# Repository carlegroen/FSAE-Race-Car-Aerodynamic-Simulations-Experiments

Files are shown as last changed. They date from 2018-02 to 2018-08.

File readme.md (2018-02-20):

# Bachelor Project: Aerodynamic design, simulations and experimental testing of a race car rear wing
- A bachelor project by Steffan Johan Kirk and Carl-Emil Grøn Christensen
- Supervisors: Jens Walther, Robert Mikkelsen

[Our formula student team's website](http://eventure.elektro.dtu.dk)

[Us in the competition]()

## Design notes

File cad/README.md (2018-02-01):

#CAD drawings for the project can be found here.

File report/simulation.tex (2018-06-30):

% !TEX root = main.tex
\chapter{Simulation}
\label{chap:simulations}

  The simulation will run in several parts. First, the wings relative placement between each other will be optimized in a 2-dimensional environment. This involves, $x$- and $y$-distance between the multi-element wings, angle of attack and height relative to the chassis to give a good estimate of the wings placement range. Secondly, a 3-dimensional analysis of the entire wing with endplates will be performed to compare with results from the wind tunnel test. %Endplate dimensions will be optimized, and further optimization of the height relative to the entire chassis to finalize the design and placement.

\section{Star-CCM+}
  Star-CCM+ was used to run the simulations of the wing first in the windtunnel for verification. As meshing and running the simulations were heavy computational tasks, the computations were run on the \emph{Niflheim Linux cluster supercomputer}, which is installed at the Department of Physics at DTU.

  The program numerically solves the Navier-Stokes equations, which are derived by the conservation of energy, mass and momentum through a volumetric flow. As Star-CCM+ uses the finite volume method, the equations are discretized to the conservative form: The in- and outgoing flux through a control volume must be conserved. Mathematically, this is expressed as:

  \begin{align}
    \frac{\delta}{\delta t} \iiint Q dV + \iint F dA = 0
  \end{align}
  Where $Q$ is the vector of the conserved variables (eg. $\rho =$ density), $F$ is the vector of fluxes(eg. $\rho u =$ mass flux, $\rho u^2 + p=$ momentum flux + pressure force) and $V$ is the control volume element and $A$ is the surface area of the control volume element. The turbulence model Star-CCM+ employs is a K-epsilon turbulence model which is the most commonly used in computational fluid dynamics. %The equations Star-CCM+ solves are the turbulent kinetic energy $k$:
  %\begin{align}
  %  \frac{\delta (\rho k)}{\delta t} + \frac{\delta (\rho k u_i)}{\delta x_i} &= \frac{\delta}{\delta x_j} \left(\frac{\mu_t}{\sigma_k}\frac{\delta k)}{\delta x_j}\right) + 2\mu_t E_{ij}E_{ij}-\rho \epsilon
  %  \intertext{and the dissipation $\epsilon$:}
  %  \frac{\delta (\rho \epsilon)}{\delta t} + \frac{\delta (\rho \epsilon u_i)}{\delta x_i} &= \frac{\delta}{\delta x_j} \left(\frac{\mu_t}{\sigma_\epsilon}\frac{\delta \epsilon)}{\delta x_j}\right) + C_{1\epsilon} \frac{\epsilon}{k} 2\mu_t E_{ij}E_{ij}-C_{2\epsilon}\rho \frac{\epsilon^2}{k}
  %\end{align}

  The reader interested in how Star-CCM+ works is referred to the \emph{User Guide Star-CCM+, version 13.02}.

\section{Mesh Generation}
\label{sec:mesh}

  The mesh has to be structured in accordance to best practice. Areas with high velocity and pressure gradients have to be dissolved in acceptable resolutions, in order to ensure correct results. Running an initial test on a generic mesh made it clear where the volume mesh requires greater resolution. Gradients are easily visible around the wing's leading edge, and generally around the solid bodies. Furthermore, aligning the mesh with the flow improves accuracy and rate of convergence. To determine the convergence of simulation results, six different mesh resolutions were used to examine the simulations for the wind tunnel setup with a wind velocity of $\SI{40}{\metre\per\second}$. Finding the minimum mesh resolution where results have converged with higher resolution results, means a minimum computation time can be achieved and thereby allowing for more simulations to be run.

  \begin{figure}
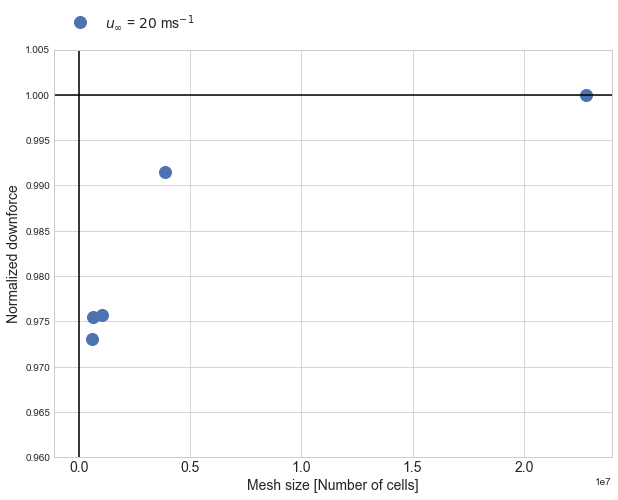
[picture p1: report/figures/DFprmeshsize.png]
    
    \caption{Normalized downforce as a function of mesh size. Plotted to see the convergence towards the same force.}
    \label{fig:DFprmeshsize}
  \end{figure}

  \begin{figure}
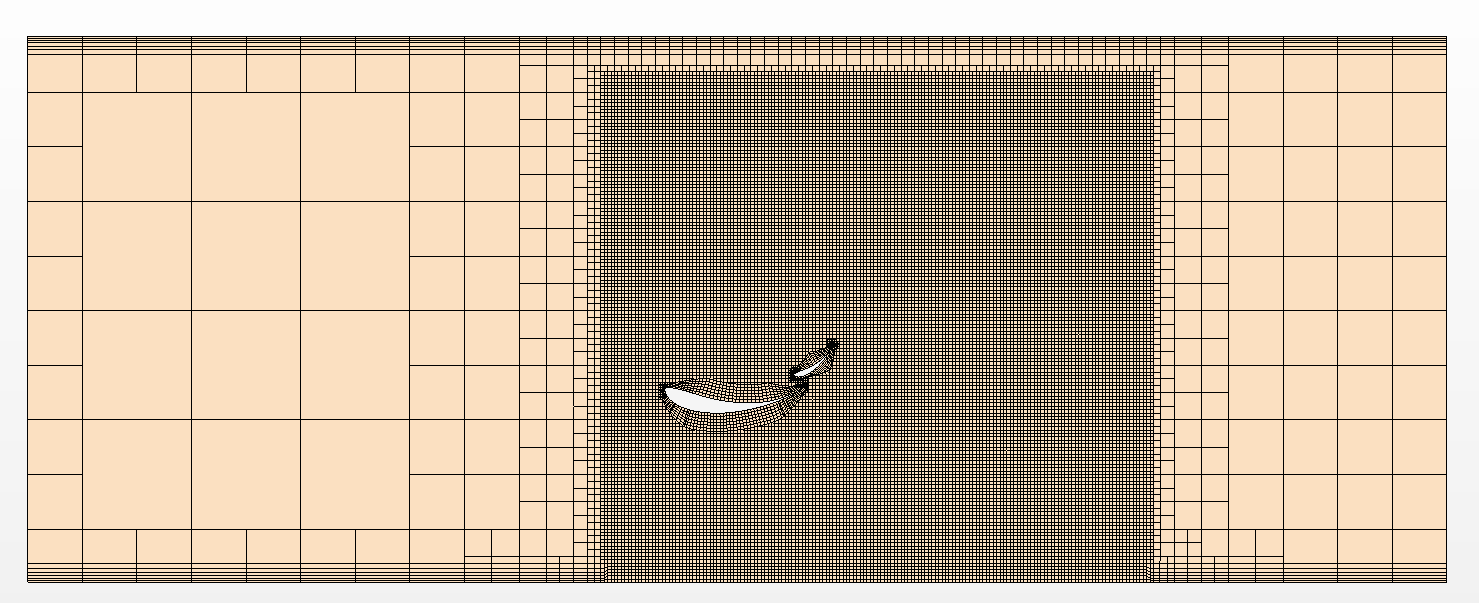
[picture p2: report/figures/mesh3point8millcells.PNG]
    
    \caption{2D cut through of the volume mesh used for simulations of the wind tunnel test. Mesh size is approximately $0.4 \cdot 10^{7}$ cells.}
    \label{fig:mesh3point8mill}
  \end{figure}

  Generating a mesh of correct size is done by sampling downforce over a range of mesh sizes. In figure \ref{fig:DFprmeshsize}, the normalized downforce is plotted as a function of the mesh size. The mesh independence study shows that the function converges to acceptable levels near the mesh size $\SI{.4E7}{}$, and serves as a good compromise between results and computing time.

  \section{Verification of Simulation Results}
  \label{sec:simulationcomparison}

  The data from the experimental test with the $\frac{1}{4}$ scale model was first plotted to obtain an idea of the surface pressure distribution on the test wing. An example of a mean over 3000 pressure readouts for a wind speed of $\SI{40}{\metre\per\second}$ is shown in figure \ref{fig:surfacepressureint}, with the standard deviation shown as error bars. Measurements were run in wind tunnel from $\SI{10}{\metre\per\second}$ to $\SI{60}{\metre\per\second}$ in steps of $\SI{10}{\metre\per\second}$.

  \begin{figure}
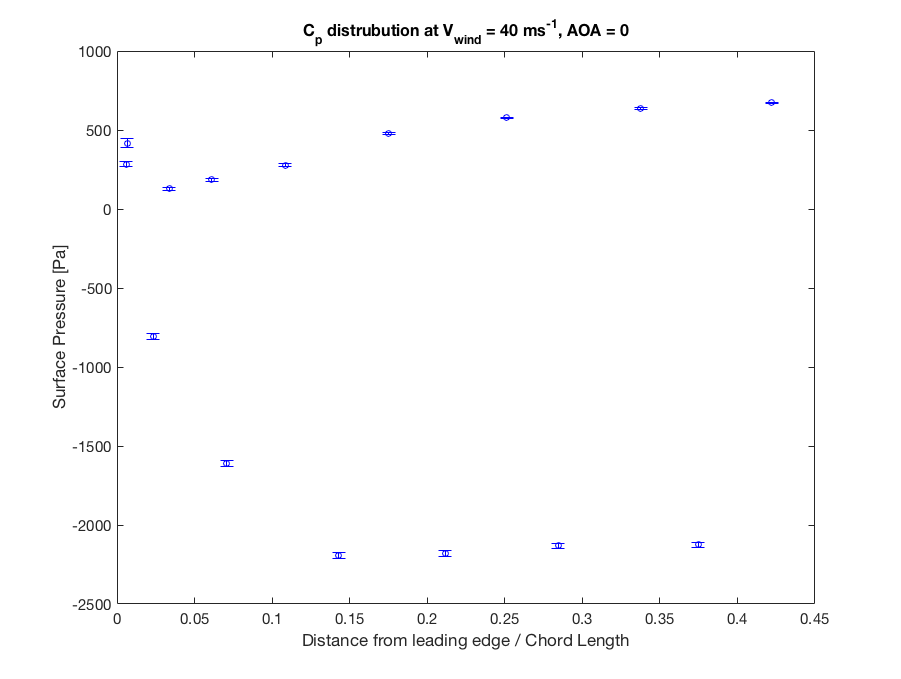
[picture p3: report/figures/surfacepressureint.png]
    
    \caption{Surface pressure readout from the 15 pressure taps located on the model at wind speed $\SI{40}{\metre\per\second}$ in the wind tunnel. Pressure readout is meaned over 3000 measurements and shown with error bars representing the standard deviation of the measurements.}
    \label{fig:surfacepressureint}
  \end{figure}

  Simulations were then run in Star-CCM+. First, the CAD model of the $\frac{1}{4}$-scaled wing was imported into the software, then the dimensions of the red wind tunnel was drawn and the CAD model was placed in the same location as in the real test. The setup was then volume meshed with a cell count of around $\SI{.4E7}{}$ cells as found in section \ref{sec:mesh} to be adequate for convergence of results. A 2D view of the volume mesh is shown in figure \ref{fig:mesh3point8mill}. After meshing, the physics model for the simulation is setup, and simulations are run for the different wind velocities.

  The 3-dimensional simulations were run until the simulation results converge. Monitors of the drag force and downforce for the wing found by the simulation were used to determine the convergence of the results, an example of the convergence plot is shown in figure \ref{fig:downforcemonitor}. Furthermore, scalar views and vector views of the pressure distribution and wind velocity around the wing profile can visually help verify that the solutions does not have any obvious faults, such as areas with extremely high velocity og pressure indicating the found solutions are not realistic. Examples of a scalar view for the pressure distribution and a vector view of the wind velocity are shown in \ref{fig:pressureScalarV40} and \ref{fig:velocityScalarV40}.

  \begin{figure}
    \centering
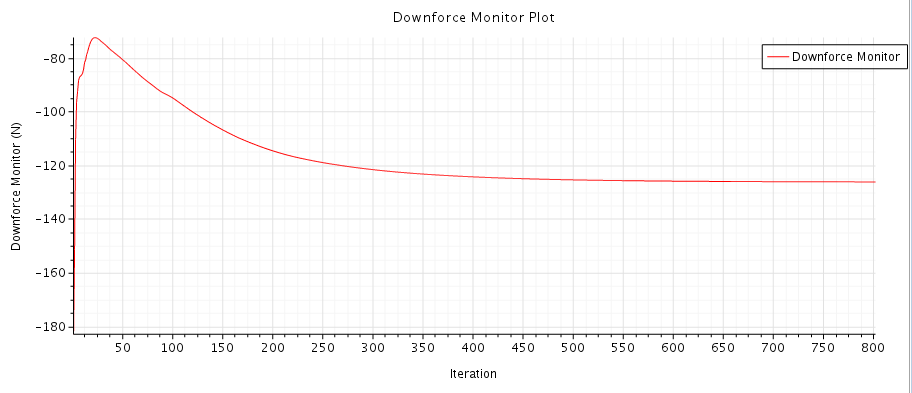
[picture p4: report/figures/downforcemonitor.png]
    
    \caption{Monitor of the convergence of the downforce over the number of iterations in Star-CCM+, here shown for a wind velocity of $\SI{40}{\metre\per\second}$.}
    \label{fig:downforcemonitor}
  \end{figure}

  \begin{figure}
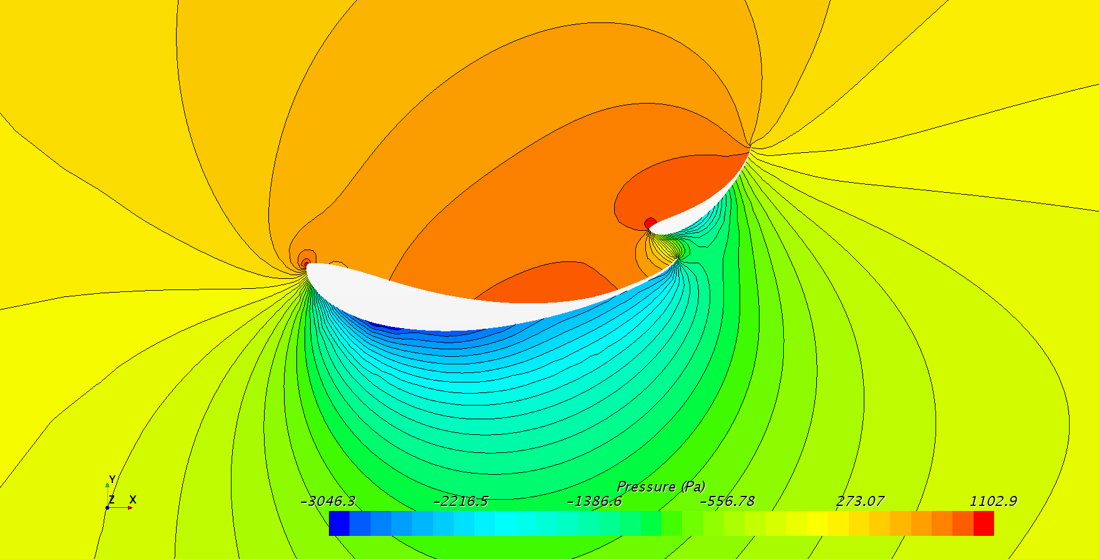
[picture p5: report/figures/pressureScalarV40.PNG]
    
    \caption{Scalar view of the pressure distribution surrounding the two elements of the wing, here at a wind velocity of $\SI{40}{\metre\per\second}$.}
    \label{fig:pressureScalarV40}
  \end{figure}

  \begin{figure}
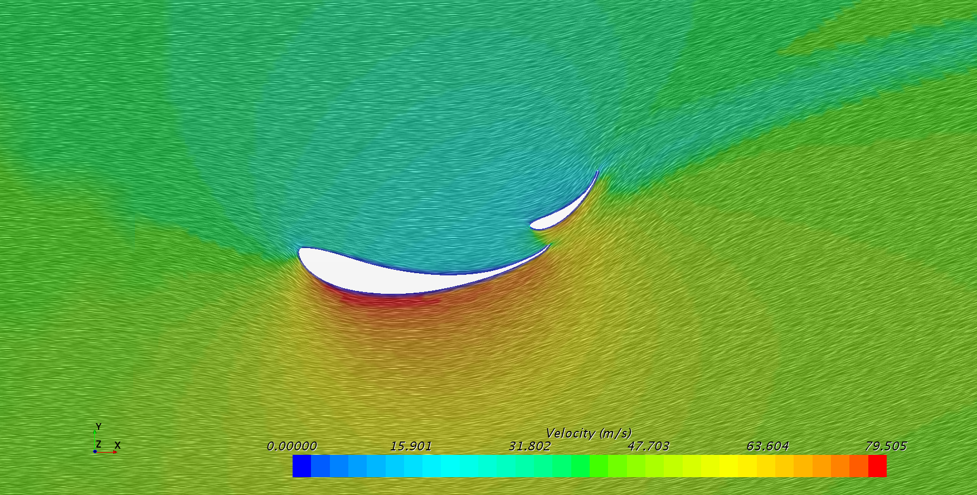
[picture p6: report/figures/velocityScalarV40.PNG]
    
    \caption{Vector view of the wind velocity surrounding the wing, here at a wind velocity of $\SI{40}{\metre\per\second}$.}
    \label{fig:velocityScalarV40}
  \end{figure}

  From the simulations the surface pressure of the airfoils was also found, and saved to compare with the measurements of the surface pressure from the real wind tunnel test. The simulated surface pressure is shown in figure \ref{fig:simsurfacepressurev40}.

  \begin{figure}
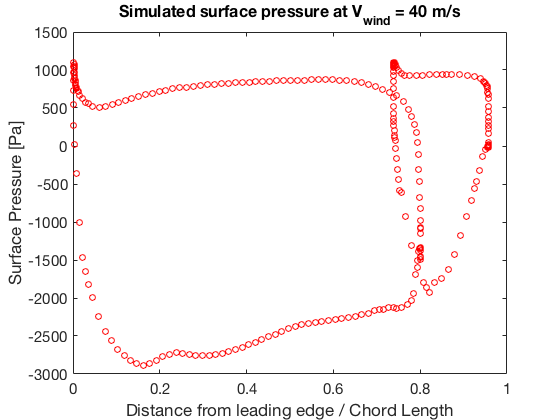
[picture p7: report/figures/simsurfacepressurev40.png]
    
    \caption{Simulated surface pressure on both elements of the wing. To the left: the larger elements surface pressure and to the right the smaller elements surface pressure is shown. Simulated at wind velocity of $\SI{40}{\metre\per\second}$.}
    \label{fig:simsurfacepressurev40}
  \end{figure}

  Comparing the surface pressure predicted by the simulation, figure \ref{fig:simsurfacepressurev40}, and measured in the test, figure \ref{fig:surfacepressureint}, show that the pressure values are not close. Furthermore comparing the by simulation predicted downforce and measured in the test downforce, shows that the simulated results predict a $\SI{40}{\%}$ higher amount of downforce than measured. This could be caused by several factors. One factor could be the assembly of the test wing is not a perfect replica of the full scale wing, an improvement to help this would be by producing the scaled model completely by machining with small tolerances, compared to the half machined and half hand-build model used in these test. This could cause the relative position of the two wing elements to be different from the CAD model used in simulations.

  Finding the correct correlation between the estimated downforce and exact surface pressure will not be possible in this report. The simulations and measurements can however be compared by using the dimensionless number, the pressure coefficient,

  \begin{align}
    C_p \equiv \frac{p-p_{\infty}}{\frac{1}{2}\rho_{\infty}V_{\infty}^2},
  \end{align}

  where $p$ is the static pressure at the point being evaluated, $p_{\infty}$ is the static pressure in the freestream, $\rho_{\infty}$ is the freestream fluid density and $V_{\infty}$ is the freestream velocity of the fluid. The pressure coefficient describes the relative pressure throughout a fluid in movement. The highest possible for $C_p$ is $1$, which occurs at the stagnation point, where the fluid comes to a complete stop. In many situations the pressure coefficient near a body is independent of the size of the body.

  The pressure coefficient therefore allows us to compare the form of the relative pressure between the simulations and the experimental test. This comparison is shown in figure \ref{fig:CpV40}. When comparing the two, a difference in value is still visible due to the difference in absolute pressure, but the form of the two $C_p$ distributions, confirm the characteristics of the flow around the wing is obtained through the simulation. A higher resolution of measuring taps would help further testing, but for the smaller model is very difficult to achieve due to lack of space.

  \begin{figure}
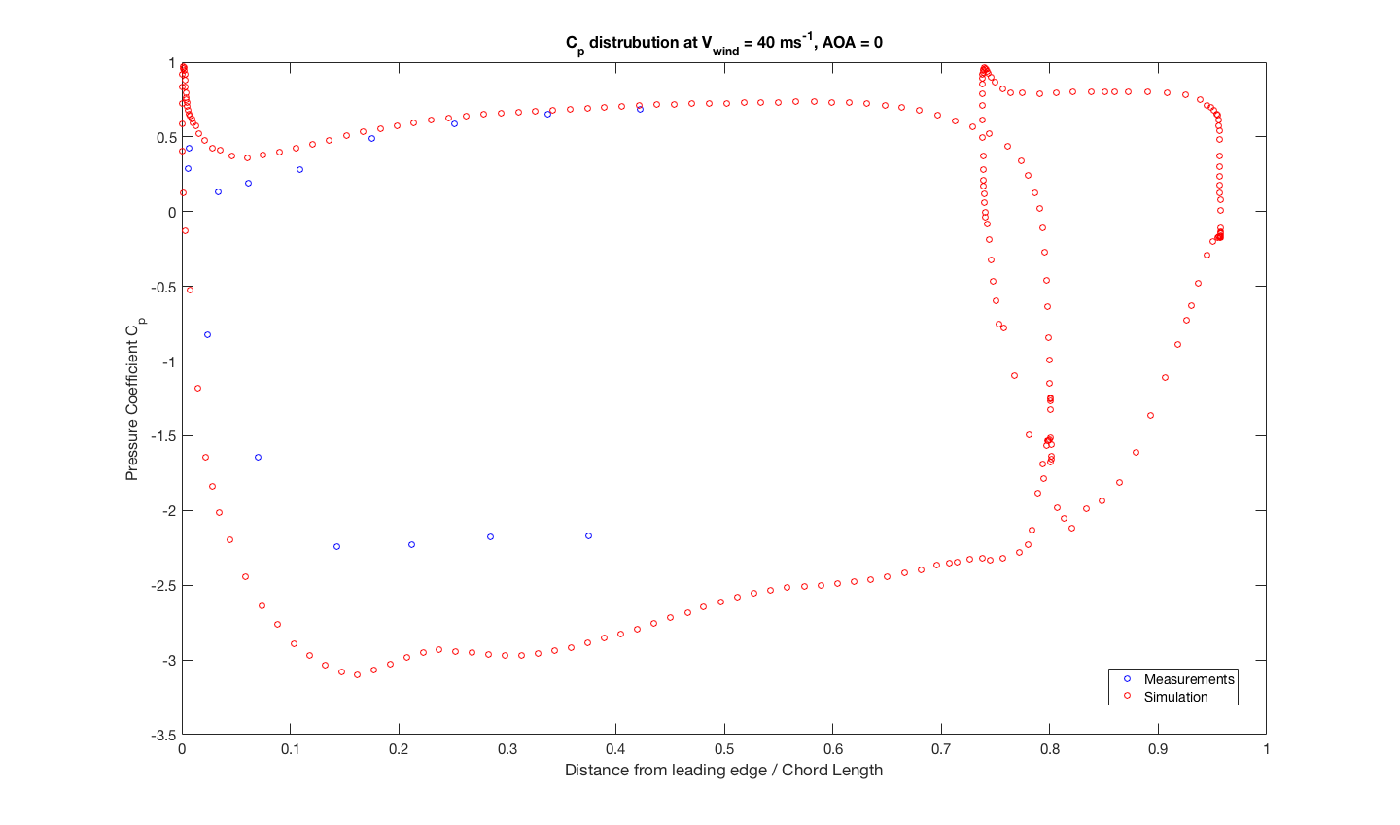
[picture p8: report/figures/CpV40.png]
    
    \caption{Comparison of simulated and test found $C_p$ values at a wind velocity of $\SI{40}{\metre\per\second}$.}
    \label{fig:CpV40}
  \end{figure}

  The use of simulations for designing an aerodynamic package for the race car for the moment is useful as a way to ensure the relative pressure distribution around the wing is as wanted, and ensuring that the flow does not separate at unwanted locations. However further work on the correlation between simulated downforce and measured downforce is still needed and the work will continue with the Vermilion Racing team, in order to have the best possibilities to design a good aero-package before having to build it.

  Lastly worth noting is that when the simulated flow is visualized by streamlines, the vortex generation at the rear of the wing, as mentioned in section \ref{subsec:endplates}, is shown clearly in figure \ref{fig:simvortex}. It is clear that the size of the produced vortices are interacting with the side walls of the wind tunnel. A suggestion for further testing of an wing with such large vortex generation would be to use a wind tunnel with a larger cross-section to avoid interactions with the side walls.

  \begin{figure}
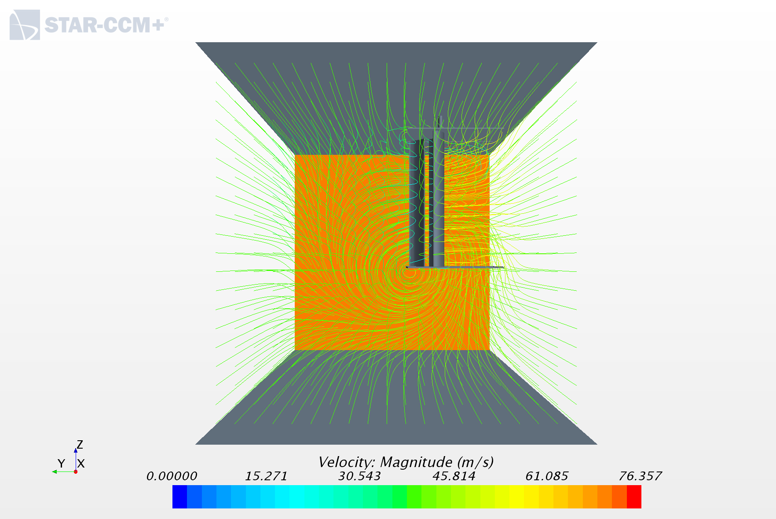
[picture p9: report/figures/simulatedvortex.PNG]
    
    \caption{Visualization by streamlines of the simulated airflow around the wing. Vortex generation at the rear of the wing is visible.}
    \label{fig:simvortex}
  \end{figure}

  \subsection{Multi-Element Wing Optimization}
  The influence of the two wing elements relative position on lift was examined to optimize the downforce further. This relative position optimization was performed in the software package \emph{MultiElements Airfoils} provided from \emph{Hanley Innovations}. A scatterplot of the relative position is seen in figure \ref{fig:multieleoptimization}. The trailing edge of the first element is seen as the dark outlines, and the position of the second element's leading edge is plotted, where the resulting lift coefficient is embedded as color. The redder the better lift coefficient. After sweeping, a maximum lift of $C_L = 2.60$  at $u = \SI{15}{\metre\per\second}$. is found with the leading edge of the secondary element placed at $x=\SI{0.5}{\metre},y=\SI{-0.01}{\metre}$ relative to the leading edge of the main element.

  \begin{figure}
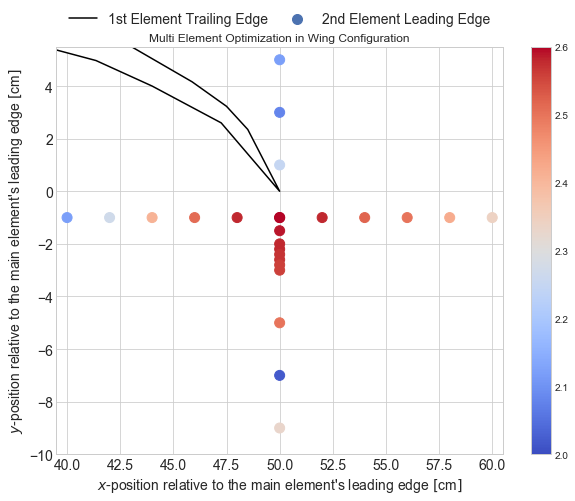
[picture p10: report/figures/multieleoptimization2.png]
    
    \caption{Optimization of the two element wing. The redder the dots, the higher the lift coefficient.}
    \label{fig:multieleoptimization}
  \end{figure}

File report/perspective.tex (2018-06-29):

% !TEX root = main.tex
\chapter{Perspective}
\label{chap:perspective}

The Eevee has to be rebuilt next year, and in order to help the effort along for future students, a list of potential upgrades are listed below, as well as a quick overview of how to improve pre-production design.

\section{Simulations}

For optimizing the design of the rear wing, using software such as CAESES allows for very quick optimization of parameters - something that would be essential to bring into the routine. Thereto, creating a full aerodynamic package with both body panels, driver, front wing and rear wing is essentialf or optimizing the entire car. Ground effects and the open wheel structure can also greatly change the lifting abilities of the car, which is why simulating the entire vehicle is important.

\section{Drag Reductive System}

A drag reductive system (DRS) is well-known from Formula 1, and has in the recent years been gaining traction (or lack therof) in the Formula Student. It is a natural extension to the aerodynamics of the car, as Formula Student has much less restrictions on aerodynamics than Formula 1. Automatically adaptive DRS, that measures the car's relative downforce and the angle of the steering column could give a big edge on straights, as flipping the wing up to reduce drag increases the top speed.

\section{Slats, Flaps, Gills and Cutaway}

%https://www.jmranalytical.com/single-post/2017/04/06/Rear-Wing-Investigation

We already have a multi element wing, but increasing the amount of elements increases the amount of downforce we can pull out of the same design. Thereto, adding slats, will allow for even higher angles of attack, albeit not increasing the $C_L$ further.

Cutting away some of the wing's end plate can also introduce beneficial vortices, or alter the way air flows over the plates. 

\section{Suspension Integration}

For optimum grip, having the rear wing press down directly on the tyres would be a great addition. Implementing a mount directly in the upright is the optimum solution, and with a low enough wing weight, adding extra unsprung mass is not a big issue.

\section{Load Distribution}

As mentioned in chapter \ref{chap:vehicleperformance}, load distribution is essential to the car's handling. If the lift coefficient differs too much between the front- and rear wing, the car's center of pressure will move with speed. This is very unattractive for inexperienced drivers, for which the competition require us to be.

\section{Pre-preg Carbon Fiber}

While the hand layup went well, moving on to pre-preg carbon fiber mattes will make for an even stronger wing with less weight. Thereto, fiber direction is guaranteed to be optimum, making for a safer product.

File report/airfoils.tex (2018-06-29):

% !TEX root = main.tex
\chapter{Airfoils and Inverted Wings}

Achieving a large negative lift coefficient $C_L$ can be done in many ways. Inspecting race cars throughout the years show that airfoils have been used as early as 1966 when Jim Hall attached a rear wing to his Chaparral 2E \cite{hucho}. Since then, the inverted wings have been a staple in the racing industry with various three dimensional geometries affecting the overall performance even further.

This chapter covers the pressure distribution of various airfoils, the selection criterions of the competition, three dimensional geometrical effects and the tools of the optimization trade.

\section{Airfoil theory}

  \begin{figure}
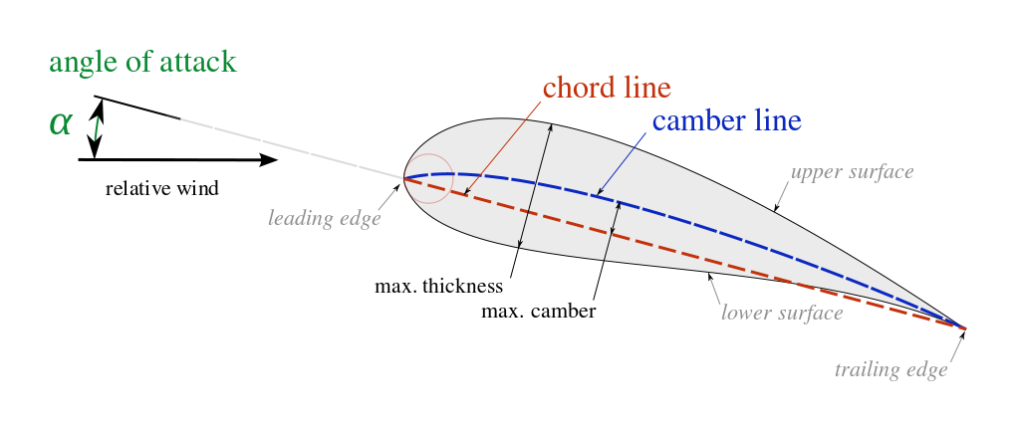
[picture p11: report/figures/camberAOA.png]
    
    \caption{Figure explaining angle of attack, chord line, camber line, upper surface (suction surface), lower surface (pressure side), leading edge and trailing edge. Figure taken from \cite{wikicamberAOA}.}
    \label{fig:camberAOA}
  \end{figure}

  An airfoil is the 2-dimensional cross section of a wing, that is defining of the wing's lifting characteristics. It is important to know the nomenclature, which is shown on figure \ref{fig:camberAOA}: The leading edge is  the most forward point of the wing, the trailing edge is the most rearward point of the wing. Camber is how much the wing the wing \emph{bends}.

  \begin{figure}
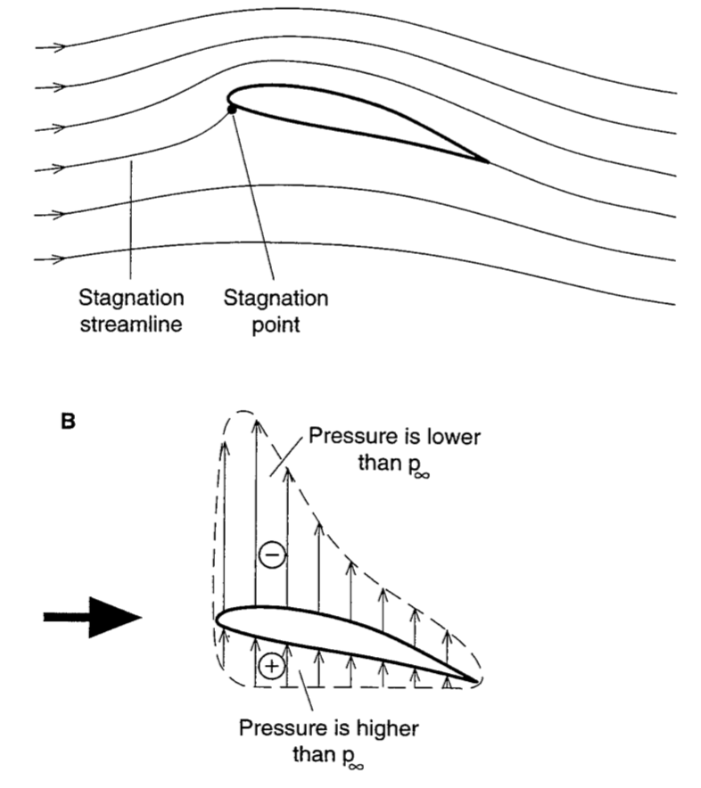
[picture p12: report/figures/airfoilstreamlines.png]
    
    \caption{A figure showing the streamlines around a slightly cambered airfoil, along with its pressure distribution below. Figure taken from \cite{jkatz}.}
    \label{fig:airfoilstreamlines}
  \end{figure}

  When an airfoil moves in a fluid, the streamlines of the particles move as seen in figure \ref{fig:airfoilstreamlines}. The streamline stops at the stagnation point, which is usually the leading edge. The other can be divided into two categories, as the flow can only go to two places: The \emph{suction surface} and the \emph{pressure surface}.

  The suction surface is the surface where the flow accelerates to high velocities and the pressure drops. This can be seen on the top part of figure \ref{fig:airfoilstreamlines}, where the corresponding pressure distribution can be seen below as the (-) part. A peak of very low pressure can be found near the leading edge, which is often called the suction peak.

  The pressure surface is the surface where the flow decellerates to lower velocities and the pressure increases. This is the bottom part of \ref{fig:airfoilstreamlines}, which provides a much lower force from the pressure than the suction side.

  The resulting changes in pressure forces the wing upwards, creating lift. It it important to note, that the suction side contributes considerably more to lift in most cases \cite{jkatz}.

  \subsection{Airfoil Lift and How to Increase it}

    Increasing the lifting capabilities of an airfoil can be done in several ways.

    First, the angle of attack of air airfoil usually increases lifting characteristics of a wing, until reaching a certain threshold where it falls off. An airfoil carries its lifting abilities usually while flow is attached - that is, where the streamlines follow the shape of the airfoil. If the flow separates from the surface of the airfoil, the lift behaviour becomes unpredictable. This effect is called \emph{stalling}.

    There are two types of stalling: Leading edge separation which are quite abrupt and greatly decreases lift, and trailing edge separation, which gradually reduces the lift. These are called a hard and soft stall, respectively. Thus, a soft stall is preferred in racing, as a hard stall will instantly change the car's handling abilities.

    Secondly, another way of changing the lift is by creating an effective change in angle of attack: Changing the wing's camber. The trailing edge of an airfoil's camber-line is the largest contributor to lift. By changing the camber geometry, the lift can be changed greatly, and the largest increase is found in the trailing edge region. This is why the introduction of flaps is prominent in both aircraft and race car wings.

    Lastly, the thickness of the airfoil affects lift up to a certain point, and the optimum thickness is about $12\%$ of the camber length. For the interested ready, reference \cite{jkatz} explores this further.

  \subsection{Reynolds Number, Lift and Drag Coefficient}

    The Reynolds number is an dimensionless number that is used to predict the flow of fluids in different flow configurations. In general the Reynolds number is used to predict if a flow is laminar or turbulent. The Reynolds number is defined as:

    \begin{align}
      Re \equiv \frac{u_{\infty}L}{\nu},
      \intertext{where $u_\infty$ is the velocity of the fluid, $L$ is a characteristic length, for an airfoil this would typically be the chord length, and $\nu$ is the kinematic viscosity of the fluid.} \label{ReynoldsNumber}
    \end{align}

    The usage of Reynolds number when designing an airfoil is the fact that the flow is similar for different scales of the same model if the Reynolds number is the same. Thereby a smaller model can be built and tested at a higher velocity that the full scale, thereby amounting to the same Reynolds number and fluid flow characteristics.

    The lift coefficient is a dimensionless coefficient that relates the lift generated to the fluid the airfoil moves in, the velocity of the fluid and the reference area. This coefficient is defined as:
    \begin{align}
        C_l &\equiv \frac{F_l}{\frac{1}{2} \rho {u_\infty}^2 c}
        \intertext{Where $F_l$ is the lift per unit width, $\rho$ is the density of the fluid, $\dot{x_\infty}$ is the velocity of the surrounding fluid and $c$ is the chord length. For a specific wing, that is, where an airfoil has a physical extension, the lift coefficient is defined as:}
        C_L &\equiv \frac{F_L}{\frac{1}{2} \rho {u_\infty}^2 A}
        \intertext{Where $F_L$ is the total lift force, and $A$ is the surface area. For a wing with both camber and angle of attack, $C_L$ is found by the following formula:}
        C_{L0} &= 2\pi (\alpha + \alpha_{L_0})\label{eq:CL}
    \end{align}
    where $\alpha$ is the lift per angle of attack in radians, $\alpha_{L_0}$ is the airfoil's camber, which acts as a additional angle of attack effect, also in radians. A correction of the lift due to downwash effects on low aspect ratio wings is found in the section below.

    Like lift, a dimensionless drag coefficient exist, that describes how drag is generated in a similar fashion:

    \begin{align}
      C_d &\equiv \frac{2F_d}{\rho {u}^2 A}
      \intertext{Where $F_d$ is the drag force - the component of the force that is parallel with the flow velocity \cite{nasadrag}. The induced drag created by the lifting force must also be added in order to find the total drag coefficient \cite{nasainduceddrag}:}
      C_D &= C_d + C_{d_\text{induced}}\\
      \intertext{where $C_{d_\text{induced}}$ is given by:}
      C_{d_\text{induced}} &= \frac{C_L^2}{\epsilon \pi \AR }
    \end{align}
    The derivation and explanation hereof is found in the section below.

  \subsection{Aspect Ratio and End Plates}
  \label{subsec:endplates}

    An important identifyer when describing an actual finite wing is, apart from chord length and airfoil design, the width. The definition used for describing the physical span is called Aspect Ratio, and for a rectangular wing is:
    \begin{align}
        \AR_\text{actual} &= \frac{b}{c}
        \label{eq:ARactual}
    \end{align}
    Where $b$ is the width of the wing and $c$ is the chord length.

    \begin{figure}
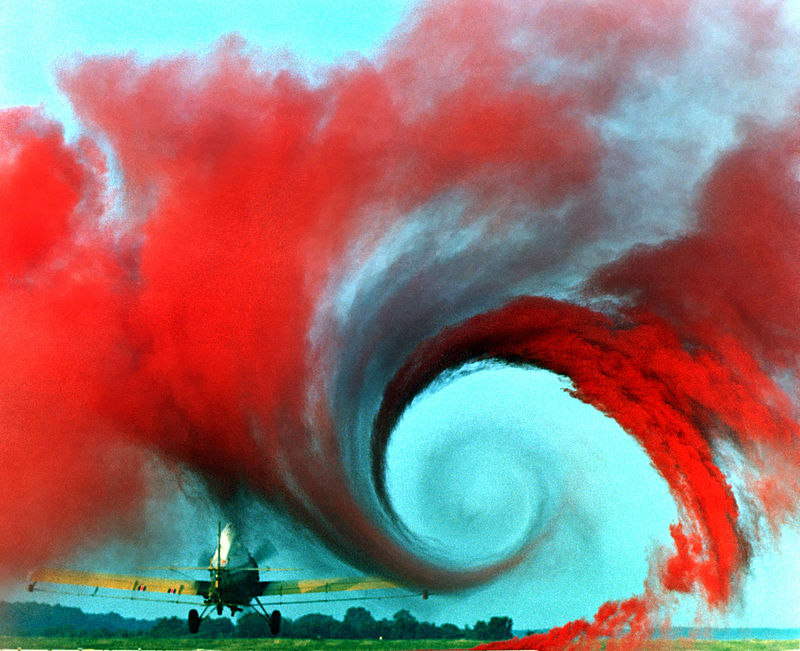
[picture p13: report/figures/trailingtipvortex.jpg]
      
      \caption{The trailing tip vortex is clearly seen to the right. Thanks to the NASA's Wake Vortex Study for the photo \cite{nasatipvortex}.}
      \label{fig:trailingtipvortices}
    \end{figure}

    The effect of having a finite length is very important in race aerodynamics. As pressure is lowered and increased on the different sides, air is going to travel around the edge of the wing in a rolling motion. This creates a vortex, which is shown in figure \ref{fig:trailingtipvortices}. The phenomenon is called tip vortices, and the magnitude of the vortex is proportional to the lift coefficient of the wing. The area these vortices cover is very large and for wings with a small span will greatly reduces the lifting powers.

    These vortices are created by an effect called \emph{downwash} when talking aeroplanes. As the wing bends the air slightly downwards, it creates an \emph{opposite force} due to Newton's second law: Lift. However, the sheet of air that passes over the length of the wing has a downward velocity component and will thus force air in that direction. This presses other air out of the way, allowing air above it to rush downwards to fill the gap. The same phenomenon is what happens at the edge of the wing, and again is what is shown in figure \ref{fig:trailingtipvortices}. When the wing \emph{bends} the airflow downward, drag is induced. While drag is almost negligible in our case, it is never wanted \cite{peterkampf}. For an elliptical wing, the induced drag coefficient is given by:

    \begin{align}
      C_{d_\text{induced}} &= \frac{C_L^2}{\epsilon \pi \AR }
    \end{align}
    Where $\epsilon = 1$ for an ellipse, and generally $\epsilon < 1$ for anything else. For a rectangular wing, $\epsilon = 0.7$ \cite{nasainduceddrag}.

    For a small aspect ratio wing, the lift coefficient has to be scaled down due to the effect of downwash.
      \begin{align}
        C_L &= \frac{C_{L0}}{1+\frac{C_{L0}}{\pi \AR}} \label{eq:liftperAR2}
        \intertext{Where $C_{L0}$ is the lift for a thin flat plate, as given in equation \ref{eq:CL} and \AR is the wing's aspect ratio \cite{nasalift2}.}
      \end{align}

    A way to combat this lift-reducing phenomenon is the addition of end plates. End plates adds a virtual additional length by adding a physical wall between the low- and high pressure surfaces. The vortices that usually go around the wing and reduce lift is severely hindered. A corrected aspect ratio can be found for wings with side plates as:
    \begin{align}
      \AR &= \AR_\text{actual}\left(1+1.9\frac{h}{b}\right) \label{eq:endplates}
    \end{align}
    where $h$ is the height of the end plate, and $b$ is the width of the wing as in equation \ref{eq:ARactual} \cite{jkatz}. The addition of end plates gives an increased aspect ratio. Inserting this back into \ref{eq:liftperAR2} shows that end plates yields an increase in lift.

    \subsection{Multiple Elements and Maximum Downforce}
      \begin{figure}[ht]
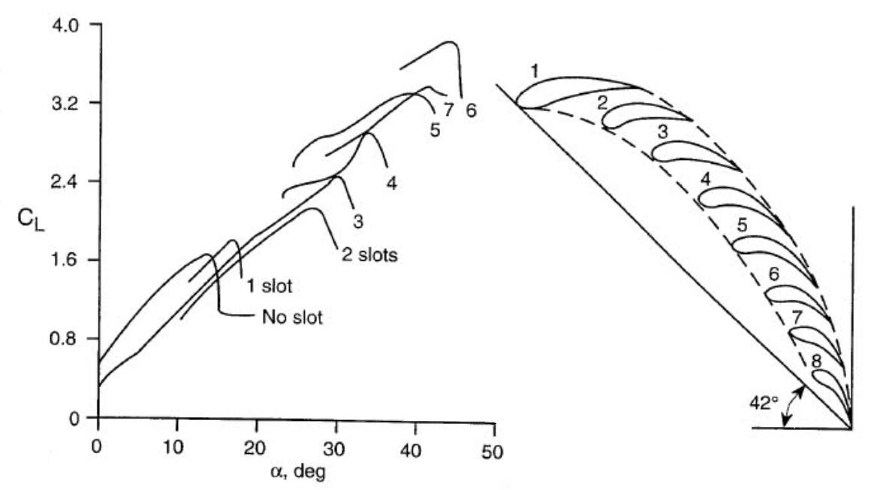
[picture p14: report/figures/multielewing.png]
        
        \caption{Lift coefficient as a function of effective angle of attack. The \emph{No slot} line corresponds to a single element wing, and the \emph{1 slot} corresponds to a double element wing. Figure taken from \cite{jkatz}.}
        \label{fig:multielewing}
      \end{figure}

      As mentioned before, in order to increase downforce on a wing (made of a predefined airfoil) there is two options: Increasing the width of the wing, or increasing the camber. As the width is fixed by regulations, the camber has to be varied. Increasing camber usually causes flow separation, but by splitting the airfoil into multiple elements, this can be circumvented while gaining effective airfoil camber. The camber attained by using multiple elements is usually much higher than with a single element, and letting the high pressure from the first element transition to the low pressure zone of the secondary element results in a favorable interaction between the two elements.

      The lift coefficient can be seen as a function of (effective) angle of attack in figure \ref{fig:multielewing}. Notice how the combined camber can be increased before stalling occurs and lift increases. A leading airfoil (also called a \emph{slat}) will extend the range of possible camber even further, but will not increase the lift curve \cite{jkatz}.

\section{Wing Parameters}

  The previous sections describe which parameters can be varied in order to attain better aerodynamical properties, such as higher lift, robustness towards stall and protection against trailing tip vortices. Improving a wing has several optimization parameters and in table \ref{tab:optimizationvars} is a list of how these are going to be handled in the following sections.
  \begin{table}
    \begin{tabularx}{\textwidth}[t]{>{\columncolor{seapurple!40}} l XX}
      \arrayrulecolor{seapurple}\hline
      \rowcolor{white}
      \textbf{\textcolor{seapurple}{Parameter}} & \textbf{\textcolor{seapurple}{Effect}} & \textbf{\textcolor{seapurple}{Optimization Technique}}\\
      \hline
      Thickness & Usually predefined by airfoil & N/A\\
      Angle of Attack & Changes lift characteristics & Finding the optimum angle of attack\\
      Camber & Usually predefined by airfoil & Adding additional Elements\\
      Position between elements & Changes lift characteristics & Optimizing $x,y$ position between elements\\
      Size & Sizes directly increases lift & Finding the maximum allowed size by regulations
    \end{tabularx}
    \caption{Table of parameters that can vary and how to optimize the parameter.}
    \label{tab:optimizationvars}
  \end{table}

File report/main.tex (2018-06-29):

% !TEX root = main.tex
\documentclass[english,a4paper,12pt,twoside,table]{memoir}
\usepackage{amsmath}
\usepackage{lipsum}
\newtheorem{lemma}{Lemma}
\usepackage[draft,english]{fixme}
\usepackage[export]{adjustbox}
\usepackage{enumitem}
%\usepackage{pgfplots}
\usepackage{nomencl}
\makenomenclature
\newcommand{\nomunit}[1]{%
  \renewcommand{\nomentryend}{\hspace*{\fill}[#1]\nolinebreak\hspace*{2cm}\mbox{}}%
}

\usepackage{babel}
\usepackage{slantsc}
\usepackage{array}
\usepackage{pdfpages}

%\setkomafont{subsection}{\usefont{T1}{fvm}{m}{n}}
%\setkomafont{section}{\usefont{T1}{fvs}{b}{n}\Large}
%\setcounter{secnumdepth}{0}
%\pagestyle{empty}
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

\nouppercaseheads
\pagestyle{main}
%%%%%%

%%%%%%
% CHAPTER PAGE STYLE
%%%%%%
% \makeoddhead{plain}{}{}{}
% \makeevenhead{plain}{}{}{}
% % sidens fod: sidetal
% \makeoddfoot{plain}{}{}{\thepage}
% \makeevenfoot{plain}{\thepage}{}{}
% \aliaspagestyle{chapter}{plain} % make chapter pages same page style as everything else

%%%%%%
% CHAPTER STYLE
%%%%%%
%\usepackage[table]{xcolor}
\usepackage{tikz}

\makechapterstyle{box}{
  \renewcommand*{\printchaptername}{}
%  \renewcommand*{\chapnumfont}{\normalfont\sffamily\huge\bfseries}
  \renewcommand*{\printchapternum}{
    \flushleft
    \begin{tikzpicture}
      \draw[fill,color=black] (0,0) rectangle (2cm,2cm);
      \draw[color=white] (1cm,1cm) node { \chapnumfont\thechapter };
    \end{tikzpicture}
  }
 % \renewcommand*{\chaptitlefont}{\normalfont\sffamily\Huge\bfseries}
  \renewcommand*{\printchaptertitle}[1]{\flushleft\chaptitlefont##1}
}
%%%%%%

% used for flow charts
\usetikzlibrary{shapes,arrows}
% Define block styles
\tikzstyle{decision} = [diamond, draw, fill=blue!10,
    text width=9em, text badly centered, node distance=3cm, inner sep=0pt]
\tikzstyle{block} = [rectangle, draw, fill=blue!10,
    text width=10em, text centered, rounded corners, minimum height=4em]
\tikzstyle{line} = [draw, -latex']

\usepackage{booktabs}
\setlength{\heavyrulewidth}{0.15em}
\setlength{\lightrulewidth}{0.08em}

% Where to look for figures
\graphicspath{ {./figures/} }

\newcommand{\mc}[1]{\multicolumn{1}{c}{#1}}
%\usepackage{threeparttable}
%\usepackage{multirow}

\numberwithin{equation}{chapter}
\numberwithin{table}{chapter}
\numberwithin{figure}{chapter}
\usepackage{varioref}
\usepackage[hidelinks]{hyperref}
\linespread{1.15}
\usepackage[sc]{mathpazo}
\usepackage{wasysym}
\usepackage{cite}
\usepackage{multirow}
\usepackage{capt-of}

\parindent 0pt
\setlength{\parskip}{2mm plus0mm minus0mm}

% Included chapters
\includeonly{
introduction,
vehicleperformance,
airfoils,
conceptdesign,
experiment,
simulation,
construction,
discussion,
conclusion,
perspective,
appendices
}

% Macros
\newcommand{\sref}[1]{Section~\ref{#1}}
\renewcommand{\fref}[1]{Figure~\ref{#1}}
\renewcommand{\tref}[1]{Table~\ref{#1}}
\renewcommand{\eqref}[1]{Equation~(\ref{#1})}
\renewcommand{\vec}[1]{\mathbf{#1}}
\newcommand{\half}[0]{\frac{1}{2}}
\newcommand{\mean}[1]{\ensuremath{\left\langle #1 \right\rangle}}
\newcommand{\pdiff}[2]{\frac{\partial #1}{\partial #2}} % Partial derivative
\newcommand{\ppdiff}[2]{\frac{\partial^2 #1}{\partial #2^2}} % Partial derivative
\newcommand{\mat}[1]{\ensuremath{\boldsymbol{#1}}}
\newcommand{\norm}[1]{|#1|}
\newcommand{\cov}[0]{\text{cov}}
\newcommand*\chem[1]{\ensuremath{\mathrm{#1}}}

\usepackage{listings}
\usepackage{color}
\usepackage{textcomp}
\definecolor{listinggray}{gray}{0.9}
\definecolor{lbcolor}{rgb}{1,1,1}
\lstset{
	backgroundcolor=\color{lbcolor},
	tabsize=2,
	rulecolor=,
	language=matlab,
        basicstyle=\scriptsize,
        upquote=true,
        aboveskip={1.5\baselineskip},
        columns=fixed,
        showstringspaces=false,
        extendedchars=true,
        breaklines=true,
        prebreak = \raisebox{0ex}[0ex][0ex]{\ensuremath{\hookleftarrow}},
        frame=single,
        showtabs=false,
        showspaces=false,
        showstringspaces=false,
        identifierstyle=\ttfamily,
        keywordstyle=\color[rgb]{0,0,1},
        commentstyle=\color[rgb]{0.133,0.545,0.133},
        stringstyle=\color[rgb]{0.627,0.126,0.941},
}
%%%%% BEAUTIFUL TABLES %%%%%
\usepackage{xcolor}
\definecolor{seablue}{HTML}{4C72B0}
\definecolor{seagreen}{HTML}{55A868}
\definecolor{seared}{HTML}{C44E52}
\definecolor{seapurple}{HTML}{8172B2}
\definecolor{seayellow}{HTML}{CCB974}
\definecolor{seacyan}{HTML}{64B5CD}
\usepackage{tabularx}

\renewcommand{\arraystretch}{1.5}
\setlist{nolistsep}

%%% Makes fonts work
\usepackage[cmintegrals,cmbraces]{newtxmath}
\usepackage{ebgaramond}
\usepackage[T1]{fontenc}

%%%%% BEGIN DOCUMENT %%%%%
\begin{document}
\pagenumbering{roman}
\pagestyle{plain}
%\input{frontpage}
\includepdf[pages={1}]{frontpagev2.pdf}
\setcounter{page}{3}
\input{preface}
\input{acknowledgement}
\input{abstract}
\input{nomenclature}

%%%%% Signature page
\newcommand{\namesigdate}[2][5cm]{%
  \begin{tabular}{@{}p{#1}@{}}
    #2 \\[2\normalbaselineskip] \hrule \\[0pt]
    {\small \textit{Signature}} \\[2\normalbaselineskip] \hrule \\[0pt]
    {\small \textit{Date}}
  \end{tabular}
}

\newpage\thispagestyle{empty}\mbox{}\newpage
\tableofcontents*
%\newpage\thispagestyle{empty}\mbox{}\newpage
\newpage
\pagenumbering{arabic}
\setcounter{page}{1}
\pagestyle{main}

%%%%% INCLUDE CONTENT FILES %%%%%

%\include{filename}
\include{introduction}
\include{vehicleperformance}
\include{airfoils}
\include{conceptdesign}
\include{experiment}
\include{simulation}
\include{construction}
\include{discussion}
\include{conclusion}
\include{perspective}
\listoffigures*
\include{appendices}

%%%%% BIBLIOGRAPHY %%%%%
\nocite{*}
\bibliographystyle{unsrt}
\bibliography{references}
\end{document}

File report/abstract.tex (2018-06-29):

% !TEX root = main.tex
\chapterstyle{abstract}
\vspace{6cm}
\chapter*{Abstract}

The ability to aerodynamically improve grip without adding a weight penalty is key to winning with race cars. High downforce is highly sought after, and the newly started Vermilion Racing Team at DTU is no exception. This work presents the theoretical arguments showing why downforce is important and numerical simulations to optimize the proposed rear wing dimensions. The numerical simulations are held up against a wind tunnel experiment, showing how misalignment of wings can greatly interfere with airflows, confirming the complexity of designing aerodynamical parts. The result is a design specifications of an easily producible rear wing with two elements and large end plates providing an improvement in cornering speeds between $3-35\%$, depending on the turn radius.

\chapterstyle{box}

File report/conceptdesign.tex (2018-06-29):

% !TEX root = main.tex
\chapter{Concept Design}
\label{chap:conceptdesign}

  The following contains the conceptual design of a rear wing based on the previous chapters. First, a walkthrough of different airfoil profiles and their benefits is followed by selection of one particular. Second, analyzing the amount of elements the wing should consists of with regards to production time and ease of construction. Third, the dimensional requirements outlined by the competition rules are given, and finally, a Product Design Specification (PDS) is set up to make sure that the design solution addresses all the problems it attempts to solve. Based on the PDS, an initial design is proposed, followed by a section describing the various possible methods of optimization.

  \section{Comparison of Airfoils}

  \begin{figure}
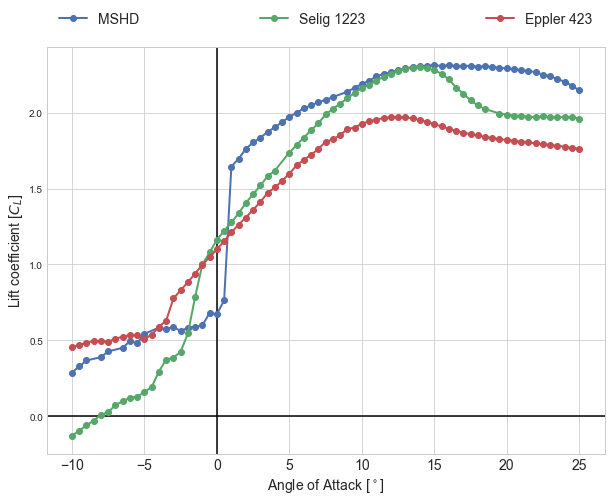
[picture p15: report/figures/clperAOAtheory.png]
    
    \caption{A comparison of the three airfoils as a function of angle of attack. The MSHD profile shows high lifting characteristics over a wide range of angles of attack. Comparisons are from XFOIL at $\text{Re} = \SI{3E5}{}$.}
    \label{fig:AOAofairfoils}
  \end{figure}

    Finding a fitting airfoil requires deep investigation of airfoil databases and articles. The requirements for this airfoil according to the PDS is a really high lift wing, operating at large ranges of Reynolds numbers, where the highest (according to track regulations) is around:
    \begin{align}
      \text{Re} &= \frac{uL}{\nu} = \frac{\SI{30.56}{\metre\per\second}\SI{0.6}{\metre}}{\SI{1.491E-5}{\metre\squared\per\second}} \approx \SI{1.2E6}{}
      \intertext{to around:}
      \text{Re} &\approx \SI{3E5}{} ~\text{at}~ \SI{15}{\metre\per\second}
    \end{align}
    which is the speed estimated for the tightest corners in the competition \cite{FSrules18}. Thereto, the airfoil should have soft stall characteristics and be very resilient to laminar separation bubbles (LSB for short. The interested reader is refered to reference \cite{jkatz}). This is done by having a large leading edge radius. The Reynolds number is an

    After a thorough research comparing high lift-low Reynolds number airfoils functioning over a wide variety of angles of attack, three airfoil are selected for further examination. The Eppler E423, the Motor Sport High Downforce (MSHD) and finally the Selig S1223. The lift coefficients can be seen as a function of angle of attack in figure \ref{fig:AOAofairfoils}.

    The MSHD performs incredibly well over a wide range of AOAs, with very low variation in lift coefficients. The MSHD airfoil is designed specifically for the Formula Student competition, which does make the choice rather obvious. The MSHD is selected for further investigation, and will be the airfoil of choice.

    Finding the right amount of elements depends on the airfoil, and based on the MSHD profile and previous studies, two elements were chosen: A main element and a scaled down flap with $35\%$ of the length of the main element \cite{winginitialangle}. The two elements will have an identical airfoil, as this is a classical way of generating successful multi element wings \cite{sameairfoilgoodidea}. This makes production time shorter, monetary cost lower and (hopefully) provides ample lift for the first generation race car.

  \section{Dimensional Requirements}

    The formula student competition has a clear ruleset dictating the dimensional requirements of aerodynamic devices. The most crucial elements are outlined below:

    \begin{tcolorbox}[colframe=seapurple,colback=seapurple!1]
      Height Restrictions:
      \begin{itemize}
        \item[T7.3.1] All aerodynamic devices rearward of a vertical plane through the rearmost portion of the front face of the driver head restraint support, excluding any padding, set to its most rearward position must be lower than $\SI{1.2}{\metre}$ from the ground.
      \end{itemize}

      Width Restrictions:
      \begin{itemize}
       \item [T7.3.2] All aerodynamic devices higher than 500 mm from the ground, must not extend outboard of the most inboard point of the rear wheel/tire.
      \end{itemize}

      Length Restrictions:
      \begin{itemize}
        \item [T7.3.3] All aerodynamic devices must not extend further rearward than 250 mm from the rearmost part of the rear tires
      \end{itemize}

      Minimum Edge Radii of Aerodynamic Devices:
      \begin{itemize}
        \item[T7.4\hphantom{.0}] All forward facing edges of aerodynamic devices that could contact a pedestrian must have a
      minimum radius of $\SI{5}{\milli\metre}$for all horizontal edges and 3 mm for vertical edges.
      \end{itemize}
      \vspace{5pt}
      \hspace*{\fill}\tiny{Rules from Formula Student UK 2018 ruleset \cite{FSrules18}.}
    \end{tcolorbox}

    The dimensional requirements from the rules was sketched on the front plane of the car's CAD drawing. This allows positioning the wing in the square seen in figure \ref{fig:cadplacement}.

    \begin{figure}
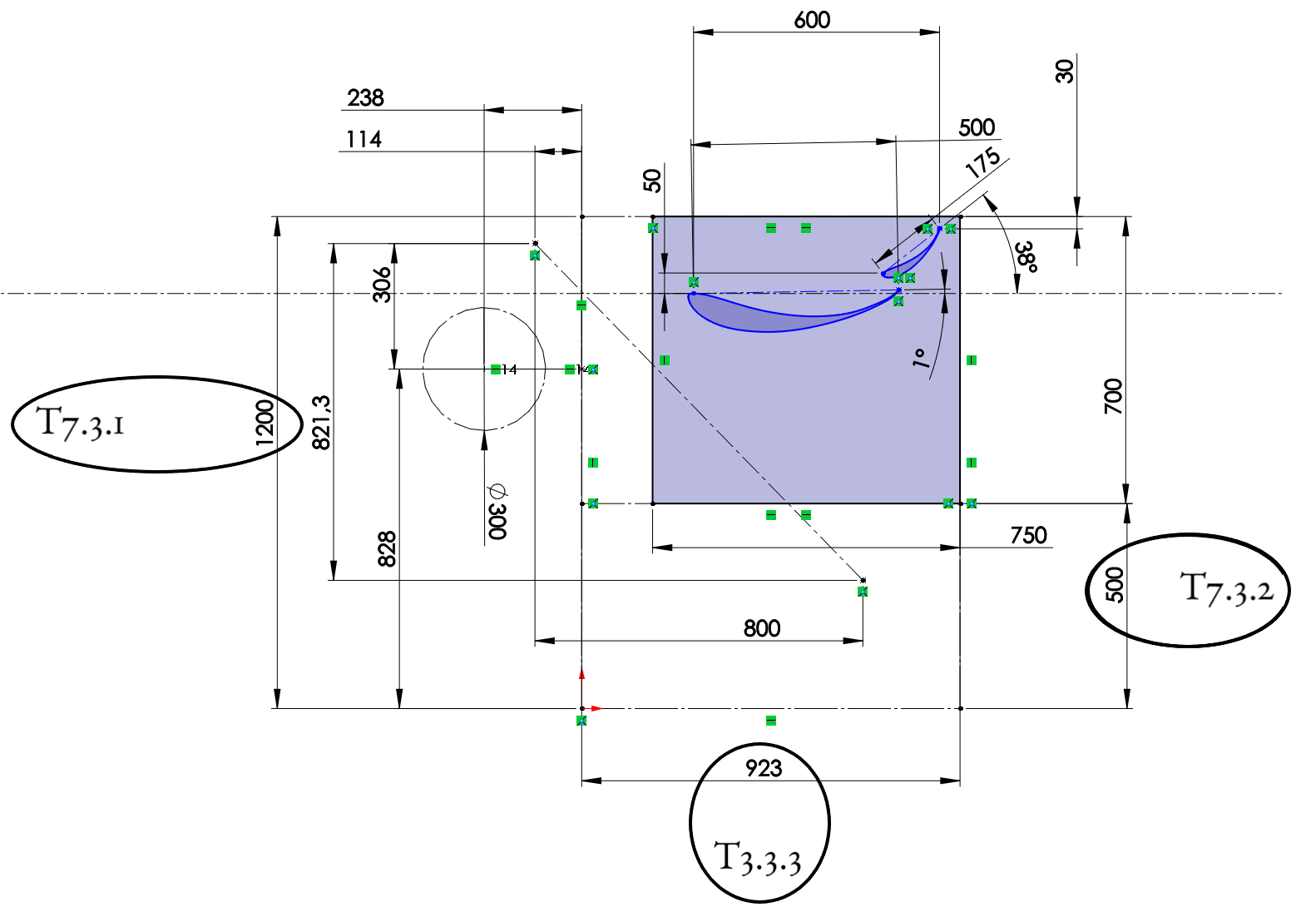
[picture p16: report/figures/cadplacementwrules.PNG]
      
      \caption{The ruleset above drawn against the design of the car. The marked square is the area where the wing can be freely placed.}
      \label{fig:cadplacement}
    \end{figure}

\newpage
  \section{Product Design Specification (PDS)}
  \label{sec:PDS}

    The PDS is a design tool created to ensure that the project solves the problems it set out to. The specifications uncovered in the previous sections are boiled down to their bare essentials, and in order to cover as large a solution space as possible, the PDS contains as few \emph{requirements} as possible. However, fulfilling the requirements is essential for a proper solution. While the criteria are not crucial, implementing the criteria are the difference between an acceptable solution and a good one. The PDS will be revised at the discussion section, in order to verify the design solution fulfills all requirements.
    \begin{table}
      \begin{tabularx}{\textwidth}[t]{>{\columncolor{seapurple!40}}l XX}
      \arrayrulecolor{seapurple}\hline
      \rowcolor{white}
      \textbf{\textcolor{seapurple}{Issue}} & \textbf{\textcolor{seapurple}{Requirement}} & \textbf{\textcolor{seapurple}{Criteria}}\\
      \hline
      Weight & Must not move CM above halfway point & As low as possible \\
      Safety & Must be in compliance with FSAE rules & Should not make handling difficult for driver\\
      Durability & Must have no fatigue limit. Must to be waterproof & \\
      Performance & Must have high downforce \& soft stall characteristic at all speeds & Should retain perfomance despite tripping. Should have end plates.\\
      Dimensioning & Must be within area defined by FSAE rules & Should allow space for motor removal. \\
      Production & Must have low time- and monetary cost & \\
      \end{tabularx}
      \caption{The PDS table shows how the final design lives up to the proposed specifications.}
    \end{table}
  \section{Initial Design}

    An initial design can be made based on the PDS and the design ideas above. The MSHD airfoil has a lot of the wanted characteristics: High downforce, both leading- and trailing edge stalls are soft, and the usable AOA-ranges are high. Furthermore, based on equation \ref{eq:endplates}, we want as large end plates as possible, which will therefore fill the entirety of the allowed area. The dimensional requirements from the FSUK rules dictate the maximum width, as shown in figure \ref{fig:cadplacement}. Finally, two elements are chosen as that gives a large amount of lift over even higher angles of attack, while being cheap timewise to construct, as seen in figure \ref{fig:multielewing}

    A first draft of the design can be seen in \ref{fig:firstdraftwing}. As the wing is intended to be optimized, a few initial assumptions were made. The first element's tail is angled $1^\circ$ below horizontal, and the angle between the two wing elements is $38^\circ$ based on a previous study \cite{winginitialangle}. The same article provides a first guess of the relative size of the two elements.

    \begin{figure}
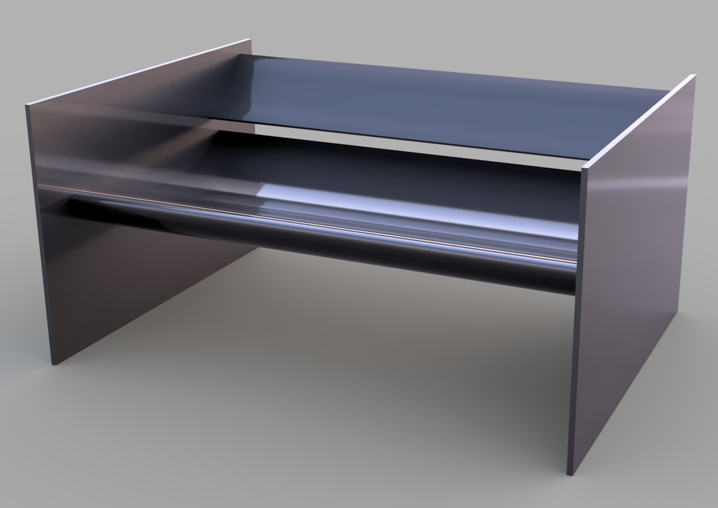
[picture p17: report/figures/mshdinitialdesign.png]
      
      \caption{Initial design of the rear wing based on the PDS and initial research. Optimization of the wing is the next step.}
      \label{fig:firstdraftwing}
    \end{figure}

  \section{Optimization Tools}

    In order to optimize a wing design, there is usually three ways employed in aerodynamics.

    Road testing might seem the easiest method of testing, but constructing full-scale rear wing and iterating is very time consuming. Furthermore, in order to measure downforce correctly, suspension vibration, varying weather and such have to be taken into account, and as this is the first car that's being produced, there is no car to test on. The unprofessional driver performance is also rarely repeatable, thus making actual road testing a time consuming and inaccurate method of testing the wings.

    Wind tunnels is another option. This allows for construction of down-scaled models, as long as Reynolds numbers are scaled accordingly. However, models can also be difficult to produce, and might not reproduce full scale results correctly. Full scale testing is expensive and wind tunnels of that size are rare.

    Lastly, computational fluid dynamics offer a method of testing a wing without actually producing anything physically. Albeit the seemingly great possibilities, computer time is also expensive, and high resolution solutions require very powerful computers \cite{jkatz}. Luckily for us, we have access to the Niflheim Linux supercomputer cluster located at the Department of Physics at the Technical University of Denmark. The supercomputer has a total of 11368 CPU cores, with 235 Teraflops of processing power.

    In order to verify the numerical models applied to the problem, a wind tunnel test will be performed on a 1/4 scale model and be compared to simulations. Post verification, numerical optimization of the wing will follow in Star-CCM+.

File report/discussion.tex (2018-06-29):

% !TEX root = main.tex
\chapter{Discussion}
  The following section will discuss the results in chapter \ref{chap:experiments},the simulations made in chapter \ref{chap:simulations} and the design in chapter \ref{chap:construction}. The purpose of this paper was to investigate the effects or aerodynamics on race cars, design a solution that would improve the car's lap time and begin manufacturing the hypothesized aerodynamic device.

  \section{Theory, Experiments and Simulations}

  The wind tunnel results plotted in figure \ref{fig:clperAOAexperiment} shows a correlation between the wing's lift and theoretical lift, assuming a constant $C_L$ for the theoretical wing. The experimental results are all lower than the theoretical, which may be due to several facts: First, the wing section's was misaligned due to the forces operating at higher speeds as one section twisted,  creating a small gap of $\SIrange{2}{3}{\milli\metre}$ between the wing sections. Secondly, the wing's extremely high lift interferes with the flow behaviour, as the wing's wake is most likely pushing air against the walls. This theory is corroborated by the simulations as seen in figure \ref{fig:simvortex}, where it is clearly seen that the wake vortex interferes with the wall's boundary layer. Third, and most likely the most important, the placement relative to each other may be slightly off. Creating a small multi element airfoil is very difficult, as placement is everything to the lift of the wing. According to the wing optimization process seen in figure \ref{fig:multieleoptimization}, very small changes can rapidly change the  lifting characteristics of the wing. This could explain why the lift of the airfoil model is much lower than the theoretical, and the fact that the simulations coincide very well with theory.

  After evaluating the experimental results and the simulations, it was clear that an investigation of the down scaled wing model was due. This revealing a relative position of the trailing-edge-to-tip position of $(x,y) = (\SI{-11.5}{\milli\metre},\SI{-8}{\milli\metre})$, instead of the planned $(\SI{-6.9}{\milli\metre},\SI{-12.5}{\milli\metre})$. The variation comes from placing the wing initially, which fits the theory mentioned in the above section. The importance of the position was not uncovered until simulations optimizing their relative position, and due to time the experiment was not redone. However, a simulation using the new relative position of the wing was performed, showing a change in lift from $ C_L = 2.50 \rightarrow 2.43$ due to misplacing the second element. Additionally, the angle of the second element is of great importance to the lift, removing in the excess of $20\%$ of the lift coefficient if wrongly placed. The lesson learned is that the second element must be very carefully placed relative to the first element, in order to not alter the flow substantially.

  This can be directly transferred to the construction of the full scale wing, making it a valuable lesson to learn in the wind tunnel.

\section{Product Design Specification Review}

  \begin{table}
    \begin{tabularx}{\textwidth}[t]{>{\columncolor{seapurple!40}}l XX}
      \arrayrulecolor{seapurple}\hline
      \rowcolor{white}
      \textbf{\textcolor{seapurple}{Issue}} & \textbf{\textcolor{seapurple}{Requirement}} & \textbf{\textcolor{seapurple}{Criteria}}\\
      \hline
      Weight & \cellcolor{seagreen!40}Must not move CM above halfway point & \cellcolor{seagreen!40}Should be as low as possible \\
      Safety & \cellcolor{seagreen!40}Must be in compliance with FSAE rules & \cellcolor{seagreen!40}Should not make handling difficult for driver\\
      Durability & \cellcolor{seagreen!40} Must have no fatigue limit. Must to be waterproof \\
      Performance & \cellcolor{seagreen!40} Must have high downforce \& soft stall characteristic at all speeds &\cellcolor{seagreen!40} Should retain perfomance despite tripping. Should have end plates.\\
      Dimensioning & \cellcolor{seagreen!40} Must be within area defined by FSAE rules & \cellcolor{seayellow!40} Should allow space for motor removal. \\
      Production & \cellcolor{seagreen!40} Must have low time- and monetary cost
    \end{tabularx}
    \caption{The PDS table shows how the final design lives up to the proposed specifications.}
    \label{tab:designreview}
  \end{table}

  The finished product have to live up to the design specification, in order to be a useful solution. In table \ref{tab:designreview}, it can be seen that all requirements are fulfilled, and all criteria except one. During the design process of the car, the removal of the engine became negligible as the battery pack is going to be removed in another way. This voids the criteria, and thus makes the solution an optimal one.

  \section{Factual Improvements}

  The theoretical lift coefficient found from simulations is shown to be $C_L = -2.8$. For a complete lap time simulation the entire aerodynamics package has to be finished. Numbers from the initial calculations of the front wing and undertray provide an estimated total lift coefficient of the car to be around $C_L = -2.4$ \cite{CLvalues}. As seen in figure \ref{fig:cornerspeedvsliftrelative}, this should increase the tight cornering speed from with $4-5\%$, while for larger radius corners upwards $20-35\%$!

  \begin{figure}
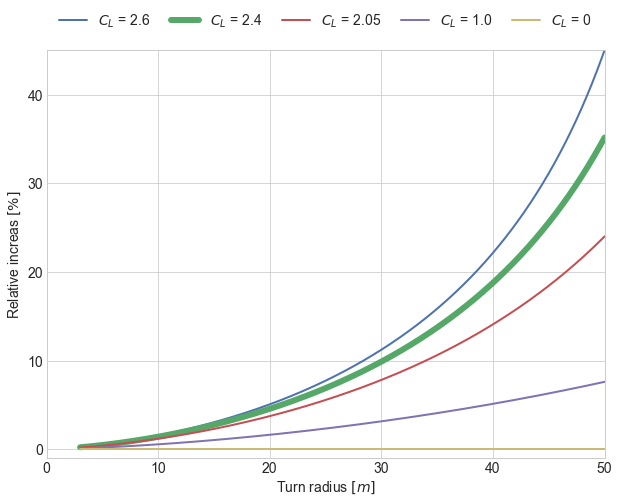
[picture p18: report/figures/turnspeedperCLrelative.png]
    \makebox[\textwidth][c]{}%
    \caption{Cornering speed as a function of turn radius for various lift coefficients, relative to a $C_L = 0$.}
    \label{fig:cornerspeedvsliftrelative}
  \end{figure}

  While fulfilling the PDS, the ease of production and being a first design ever restricted the scope of the project. Great improvements can be expected in the coming years. The extend of the theory required in order to produce a rear wing has been uncovered, and this project serves as a guideline for future iterations of the rear wing.  In chapter \ref{chap:perspective}, a series of possible improvements are evaluated and proposed for increasing the aerodynamic contribution to increasing lap times.

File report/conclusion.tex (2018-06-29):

% !TEX root = main.tex
\chapter{Conclusion}
  Vermilion Racing's rear wing has been designed based on initial research, wind tunnel experiments and simulations. Each step has been fundamental to the understanding of the importance of the theory, and will serve as a tool for future generations to expand upon.

  The rear wing's dimensions are restricted by the rules of the competition, and serve as the boundaries of the design, giving us the width and height of the wing. The wing's airfoils are chosen based on XFOIL simulations of lift profiles. Due to the nature of the competition, a highly stable wing is wanted - stalling is fatal to the car's handling abilities, which is why the highly cambered MSHD airfoil was chosen. Increasing the amount of elements greatly increases the possible angles of attack, and based on theory and time constraints, a two-element wing with identical airfoils serves as the best opportunity for increasing the lift.

  The initial concept was tested in a wind tunnel on a quarter scale model, where the results were compared to simulations. An irregularity in the results instigated further examination of the scale model, revealing a misplacement of the second wing element. After simulating their relative placement, it was discovered that relative placement is very important for lift. Therefore, new wind tunnel tests should be performed in order to verify the lifting characteristics of the wing.

  After simulating and optimizing position, a proposed design was drawn. Metallic inserts in order to reinforce the wing and physically mount it to the end plates were topologically optimized to reduce weight. The final design of the rear wing, combined with initial simulations of the remainder of the car shows to give a total down force of $C_L = 2.4$, which should give an increase in cornering speed of $3-35\%$, based on the cornering radius.

  Finally, a series of propositions for improving the rear wing design can be read in chapter \ref{chap:perspective}. Many of these should bring great improvements to the Eevee's lift characteristics.

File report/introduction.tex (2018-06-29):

% !TEX root = main.tex
\chapter{Introduction}

  \begin{figure}
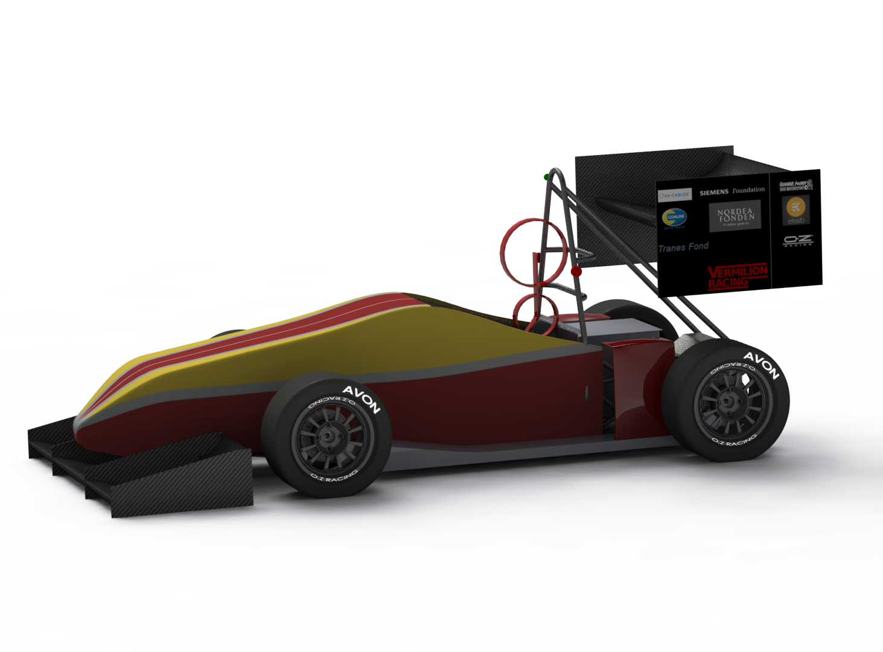
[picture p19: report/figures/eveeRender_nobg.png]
    
    \caption{The teams' race car with the conceptual design of the rear wing.}
    \label{fig:EeveeRender}
  \end{figure}

  \textsc{Vermilion Racing} is a newly started electric race car team at DTU building their very first vehicle: The Eevee \cite{bulba}. The teams' purpose is to compete against other universities at the Silverstone race track from the 11\textsuperscript{th} to the 16\textsuperscript{th} of July. As members of the team, the purpose of this report is to document the design process of the rear wing of the first car, and provide the ground works towards a full aerodynamic package for future students on the team. A render of the car's design as of the 31\textsuperscript{st} of June is shown in figure \ref{fig:EeveeRender}. As this is the first car, this project sets out to uncover the requirements, theory and know-how behind building a rear wing.

  Aerodynamics is a major decider in racing today. Cornering, not top speed is the deciding factor amongst the teams, and aerodynamics is the key. Drag, lift and side force are the three cornerstones to vehicle aerodynamics. A car's ability to handle depends on the grip of the tyres, and downforce directly increases grip by increasing the downwards load on the tyres without adding a weight penalty. Additionally, drag directly decreases the speed of a vehicle by increasing air resistance, but is of less importance as the cars of this class have far more accelerative power than the tyres can handle \cite{jkatz}. Designing the bodyworks of Eevee is therefore a dance of downforce.

  This bachelor thesis attempts to lay down the ground work for designing, optimizing and manufacturing the car's rear wing. Our advisor, Jens Honore Walther, proposed simulating the wing geometry in order to both reduce financial cost and quicken the optimization process. The objective of the numerical simulations is ultimately to create an easily producable wing in a very short timespan, that produces ample amounts of negative lift for the time spent in production.

  As this is the first year the team is designing and building a car, time and money for production is sparse. To validate the simulated optimizations, a wind tunnel test is performed on a down-scaled wing using Flow Similarity theory. The measurements are compared with the results from a computational fluid dynamics simulation performed in \emph{Star-CCM+} to verify the preciseness of the simulations. Based on this, $x$- and $y$-distance between the multi-element wings and angle of attack is then optimized for maximum downforce. The multi-element wing is taken from theoretical abstraction to reality by designing a physical wing. The position, deflection and dimensions of the wing is thoroughly described by the rules of the Formula Student competition, guiding the final design process. In the final chapter, theories regarding strength of sandwich-structured composites and carbon fiber molding are explained, in order to describe the design decisions. Finally, the end result is discussed and possible improvements to the wing and mounting system are listed.

  Measurements and tests have been carried out at the DTU Wind laboratory's Red wind tunnel with assistance from co-supervisor Robert Flemming Mikkelsen on the 19\textsuperscript{th} and 20\textsuperscript{th} of June.

  The entire project is publicly available on \url{https://github.com/carlegroen/bachelor_project_racecar_aero}, where all work files, data, various notes and CAD drawings can be found. The Formula Student team at DTU: Vermilion Racing can be followed on \url{fb.com/FSDTU}.

\section{Design Philosophy}
  Designing a car with hundreds, if not thousands of different factors is incredibly difficult. Therefore, determining which factors are most important for the car's performance is very crucial to the teams' success. As the timespan of this project is short, time sets a limitation on the complexity of the wing's dimension. In addition, since this is the first of its kind, no design decisions can be based on prior experience. Finally, the finances for building the car are tight. This forces us to choose a low-cost solution where basing the design on literature and the experience of competing teams is the ideal choice.

  The requirements for the wing are, that it has to be as low weight as possible, in order to ensure optimum acceleration of the car. Thereto, drag has to be kept low, but the effect from drag is near negligible, which will be explained in section \ref{sec:topspeed}. Lastly, we have to maximize the downforce provided by the wing. For future iterations, ensuring that the center of pressure is kept as constant as possible is essential. If the frontwing, undertray and rear wing's downforce don't scale equally with speed, the center of pressure will move during acceleration. This will make the car's handling unpredictable, and potentially limit the driver's confidence in the car.

\section{Problem Statement}

  A new aerodynamically beneficial structure is to be implemented at the rear of the Eevee with the purpose of increasing the tyre's grip without adding a weight penalty. The goal is to have a cheap, both time- and money-wise, rear wing, which provides enough negative lift to benefit the car's lap time.

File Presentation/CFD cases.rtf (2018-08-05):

Case info:

case001:
base: 0.1 m
VOR: 0.002 m
prism layers: 6
Cell count: 22.8E6
Downforce: 126.2 N
Drag: 24 N
resi:

case002:
base: 0.05 m
VOR: 0.025 m
prism layers: 6
Cell count: 6.36E5
Downforce: 123.1N
Drag: 24.6 N
resi:

iteration 2:
absolut size: 0.2
vor : 0.03 m
cells: 5.8E5
drag: 24.4 N
downforce: 122.8 N
resi: E-5

case003:
base: 0.05 m
VOR: 0.01 m
prism layers: 6
Cell count: 1.03E6
Downforce: 123.13 N
Drag: 24.5 N
V = 40 m/s
resi:

K-Omega turbulence

case004:

ase: 0.05 m
VOR: 0.005 m
prism layers: 6
Cell count: 3.87E6
Downforce: 125.12 N
Drag: 24.3 N
V = 40 m/s
resi:
236 sekunder på hver af de 24 noder

epsilon turbulence
Downforce = 125.26 N
Drag = 24.4 N

iteration 2:
max cell size 0.1m
vor: 0.0025 m
cell count:
drag:
downforce:

case005:

V = 60 m/s

case006:

V = 50 m/s

case007:

V = 30 m/s

case8 :
rette scala model med 34 grader
mesh running 18:45
Downforce = 115.6 N

run 22:13
job 59

Downforce 117 N

case 9:
full-scale
mesh 22:16
job 60
run 23:11
job 92
mesh 23:48
run 00:18
job 03
down force:
cells:

case 10:
full-scale 525
mesh 22:17
job 61
run 23:12
job 94
down:

case 11:
full-scale 350
mesh 22:17
job 62
run 23:13
job 95

case 12:
full-scale 525 2d optimised
mesh 22:18
job 63
run: 23:16
job 96

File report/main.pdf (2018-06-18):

design of rear wing of an

electric race car

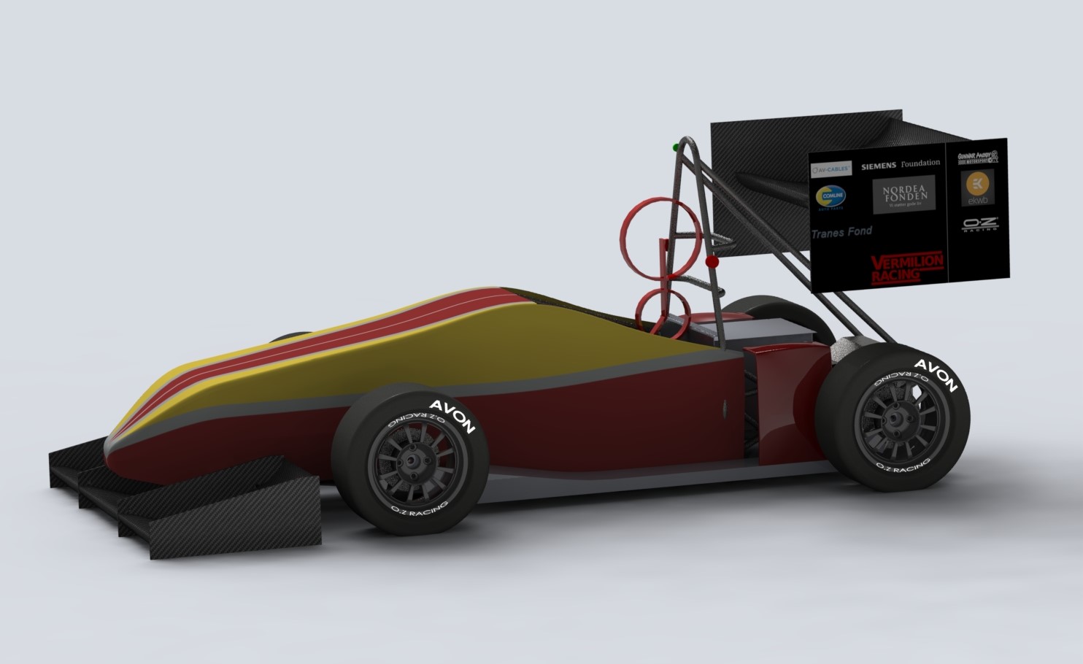
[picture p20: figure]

Steffan Johan Kirk – S170816 Carl-Emil Grøn Christensen – S170817 Department of Mechanical Engineering, Technical University of Denmark

Supervisor:
Jens Walther
Department of Mechanical Engineering, Technical University of Denmark

August 2018

# Acknowledgements

We would like to thank our supervisors Jens Walther and Robert Mikkelsen, who allowed us to work on a project we hold very dear. The project let us perform incredibly well for a first time racer at the Formula Student competition in Silverstone, and the Vermilion Racing team will hopefully live on many years ahead.

Furthermore, a big thanks to Rasmus Himborg from Philips Lighting Denmark, for helping us machine the 1/4 scale wing used in the windtunnel tests.

iii

### Abstract

Race cars wooo! Formula studee3333nt

iv

# Contents

1 Introduction | 1
2 Aerodynamic Effects on Vehicle Performance | 4
3 Airfoils and Inverted Wings | 8
4 Wind Tunnel Experiment | 9
5 Simulation | 12

vi

6 Construction | 14
7 Discussion | 17
8 Conclusion | 18
Bibliography | 20

vii

1

# Introduction

Vermilion Racing is a newly started Electric race car team building their first vehicle: The Eevee [1]. The teams’ purpose is competing against other Universities at the Silverstone race track from the 11th to the 16th .
As members of the team, the purpose of this report is to document the design process of the rear wing of the first car, the Eevee, and provide an aerodynamic package documenting drag and downforce.

Aerodynamics is a major decider in racing today. Cornering, not top speed is the deciding factor amongst the teams, and aerodynamics is the key. Drag, lift and side force are the three cornerstones to vehicle aerodynamics. A car’s ability to handle depends on the grip of the tyres, and downforce directly increases grip by increasing the downwards load on the tyres without adding a weight penalty. Additionally, drag directly decreases the speed of a vehicle by increasing air resistance, but is of less importance as the car’s in this class have far more accelerative power than the tyres can handle [2]. Designing the bodyworks of Eevee is therefore a dance of downforce.

This bachelor thesis attempts to lay down the ground work for designing, optimizing and manufacturing the car’s rear wing. Our advisor, Jens Honore Walther, proposed simulating the wing geometry in order to both cheapen and quicken the optimization process, but also gain insight into how flow in front of the rear wing affects lift performance. The purpose
of the numerical simulations are ultimately to create an easily producable
wing in a very short timespan, that produces ample amounts of negative
lift for the time spent in production. | FiXme Note: write about what has been done prior

As this is the first year the team building a car, time and money for produc-

1.1. Design Philosophy

tion is sparse. To ensure the simulated optimizations are true, a wind tunnel test is performed on a down-scaled wing using Flow Similarity theory. The measurements are compared with the results from a computational fluid dynamics simulation performed in Star-CCM+ to verify the preciseness of the simulations. Based on this, the size, x- and y-distance between the multi-element wings, angle of attack and height relative to the chassis is then optimized for maximum downforce. The multi-element wing is taken from theoretical abstraction to reality with a physical design of the wing. The position, deflection and dimensions of the wing is thoroughly described by the rules of the Formula Student competition, guiding the final design process. In the final chapter, theories regarding strength of sandwich structured composites and carbon fiber molding are handled, in order to descibe the production choices made. Finally, the end result is discussed and possible improvements to the wing and mounting system is listed.

Measurements and tests have been carried out at the DTU Wind laboratory’s Red wind tunnel with the help of our supervisor Robert Flemming Mikkelsen the 19th of June.

The entire project is publicly available on https://github.com/carlegroen/bachelor_project_racecar_aero, (https://github.com/carlegroen/bachelor_project_racecar_aero) where all work files, data, various notes and CAD drawings can be found. The Formula Student team at DTU: Vermilion Racing can be followed on fb.com/FSDTU.

### 1.1 Design Philosophy

Designing a car with hundreds, if not thousands different factors is incredibly difficult. Therefore, analyzing which things matters and which don’t is crucial to the teams’ success. First, the deadline for finishing the wing is soon. This sets a limit on the complexity of the wing’s dimensions. Secondly, this is the first iteration of the car, thus no decision can be based on prior experience, and optimization has to wait for the next iteration. Finally, the finances of the car is tight. This forces us to go with a low-cost solution. We therefore have to go for a simple, low cost wing, basing the design solely on litterature and experience other teams have done.

The wing has to have as low weight as possible, in order to ensure optimum acceleration of the car. Thereto, drag has to be kept low, but the effect from drag is near negligible, which will be explained in section 2.1. Lastly, we have to maximize the downforce provided by the wing, but also ensure that the center of pressure is kept as constant as possible. If the frontwing, undertray and rear wing’s downforce don’t scale equally

1.1. Design Philosophy

with speed, the center of pressure will move during acceleration. This will make the car’s handling unpredictable, and potentially limit the driver’s confidence in the car.

2

# Aerodynamic Effects on Vehicle Performance

The first argument to the importance of aerodynamics is based around two facts: The fact that drag is neglible in regards to the Formula Student vehicle’s top speed on straights, and the fact that aerodynamically increasing the vehicle’s effective mass due to downforce increases tyre grip, which in turn allows for higher cornering velocities.

The second part of this chapter covers the importance of centering the effective mass increase due to aerodynamic devices close to the center of gravity – otherwise handling characteristics becomes a function of velocity.

### 2.1 Drag Effects on Straights

First, let’s explain what makes a car fast, and what parameters we can
change to improve the speed of our car. The car’s acceleration can be
described by Newton’s second law as: | FiXme Note: stort D eller
| lille d i ligningen?
∑ Fx = mx¨ = F | (2.1)

Where the sum of forces in the x-direction (the direction of travel) can be
expressed as the force already pertained by the vehicle, minus the drag force:

F − CD

(
1
2

ρx˙

2A

)
= mx¨ | (2.2)

2.1. Drag Effects on Straights

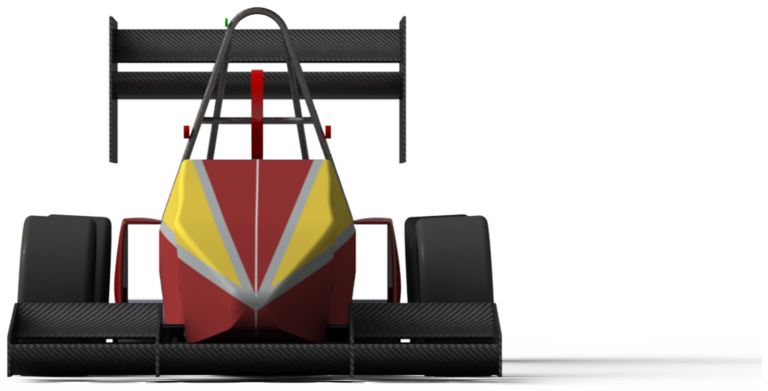
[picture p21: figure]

Figure 2.1: Frontal area of the car with a dummy wing inserted into the CAD model, in order to get an estimate of the drag coefficient CD.

Where CD is the drag coefficient of the vehicle, ρ is the density of the fluid it moves in and A is frontal area of the vehicle. Assuming we’re moving at a steady speed, the acceleration is 0, hence

F = CD

(
1
2

ρx˙

2A

)
(2.3)

As we were interested in the speed of the car, let’s solve for the velocity. The force is given by F = P
x˙

, where P is the power of the car, which gives:

x˙ =

(
2P
CD (ρA)

)1
3
(2.4)

This is assuming we’re traveling at terminal velocity – that is, the point where the Driving Force = Friction Force. The terminal velocity of the
racer is then easily calculated, as the competition restricts the maximum
amount of power to 80 kW, and the frontal area of the car is approximated
from the CAD drawing seen in figure 2.1. | FiXme Note: fix calculation to use 0.99 instead of 1.2 FiXme Note: missing radiators

x˙max =

(
2 · 80 kW
0.85 (
1.225 kg m⁻³ 1.2 m²

)

)1
3
= 50 m s⁻¹ = 181.4 km h⁻¹ | (2.5)

however, given the ruleset a forecasted maximum of 110 km h⁻¹ allows a much larger drag coefficient CD:

CD =

2P
x˙

3 (ρA)

=

2 · 80 kW
(120 km h⁻¹
)

3

(
1.225 kg m⁻³ 1.2 m²

) = 2.82 (2.6)

Thus, the car’s top speed will only be limited by a drag factor > 2.82, FiXme Note: insert source which is far above the drag introduced by the aerodynamic devices.

From this derivation, it is clear that the car’s abilities at maximum speeds
far exceed the requirement of the track. Therefore, the next step is to

2.1. Drag Effects on Straights

improve cornering speeds which depend strongly on the tyre’s grip on the surface of the road [2].

### 2.1.1 Downforce Effects on Cornering

Shown before, drag does not limit the car’s performance on straights. During cornering, drag is not an issue either, but the grip of the tyres limits the maximum velocity before the vehicle loses traction due to the centripetal force which is given by: [3]

Fcentripetal =

mx˙

2
r

(2.7)

where r is the distance to the center of the cornering circle. The frictional force the car exerts due to downforce and tyre grip is given by:

Ffriction = µFnormal | (2.8)

where the normal force is given by both the weight and (negative) lift of the car, which serves as an effective mass increase:

Ffriction = µ

(
mg +

1
2

ρCLAx˙

2

)
(2.9)

The vehicle will lose traction when the frictional force is less than the centripetal force.

mx˙

2
r

> µ

(
mg +

1
2

ρCLAx˙

2

)
(2.10)

Giving the maximum velocity for a given corner radius before the car skids out:

⇒ x˙ <

(
2µmgr

m − µCLρrA)1
2
(2.11)

Again, the forecasted variation in radii of corners is prescribed by the rules to be between 3 m to 50 m [4]. Plotting this for various CL values between 1.5 to 2.6 [5], assuming m = 300 kg, µ = 1.5 [6] and A = 0.99 m² as previously used. The result can be seen in figure 2.2.

### 2.1.2 Load Distribution

The scope of this thesis is not to incorperate a full aerodynamic package, but a quick overview of load distribution is essential to understanding the behaviour of the car.

The effective mass added from negative lift depends on the lift coefficient. It is evident that different items on the car carry different lift coefficients,

2.1. Drag Effects on Straights

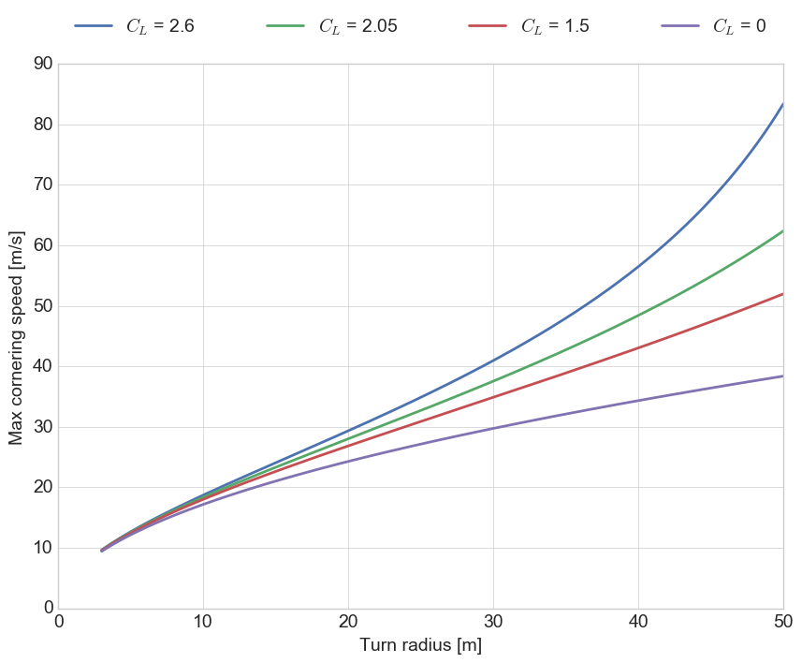
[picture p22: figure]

Figure 2.2: Cornering speed as a function of turn radius for various lift coefficients.

thus making the lifting forces over the cars length a function of relative speed. For the unexperienced driver, this is not easily managed as handling characteristics change with velocity. Therefore, it is desirable to have the aerodynamic center of pressure close to the car’s center of gravity, in order to have similar handling at all velocities. While this is not handled in this thesis, it is ideal for future iterations and essential for a full aerodynamical package.

3

# Airfoils and Inverted Wings

### 3.1 Airfoil theory

Theory of airfoils from katz book, to be written tuesday 19.

### 3.2 Comparison of Airfoils

Choosing the MSHD wing. To be written from MSHD article on tuesday 19.

### 3.3 Multi elements? How many is enough

From katz book, written tuesday 19.

### 3.4 Optimization Tools

Also from katz book to be written tuesday 19.

Building physical models is cool, wind tunnel time is expensive though

Let’s use CFD!

To make sure CFD works, we need to perform experiments to verify simulations work.

Let’s make a small scale wind tunnel test and simulate the rest!

4

# Wind Tunnel Experiment

Verifying the simulated aerodynamic effects is crucial to ensuring the correctness of the numerical analysis. In order to assess the reliability of the
previouisly conducted simulations, a physical measurement of the pressure along the down-scaled wing will provide results for comparison. FiXme Note: sounds
awful. fix

### 4.1 Aerodynamics

### 4.1.1 Similarity of Flows

In order to perform tests on the rear wing, it has to be scaled down to fit inside the wind tunnel. This reduces the physical size of the wing, which under equal circumstances changes the flow around it. In order to correctly emulate the simulated flow inside a wind tunnel, the Reynolds number and Euler number have to be the same, assuming incompressible flows:

Rem = Re | (4.1)
Eum = Eu | (4.2)

Mathematically, the Reynolds- and Euler number are defined as:

Eu =

pu − pd
pv²

(4.3)

where v is the characteristic velocity of the flow, pu denotes upstream pressure, and pd denotes downstream pressure, and:

Re =

uL
ν

(4.4)

4.2. Equipment

where u is the velocity relative to the object, L is the characteristic length
and ν is the kinematic viscosity of the fluid.

For a down-scaled model, matching Reynolds- and Euler number requires
an increase in velocity, inversely proportional to the increase in length FiXme Note: skriv det her
ud plx.

umLm
ν

=

uL
ν
⇒ um =

L
Lm
u | (4.5)

### 4.2 Equipment

- The Red wind tunnel (60 m s⁻¹

to 65 m s⁻¹
)
- 1/4 scale wing
- Syringe inserts
- Rubber tubing
- Pressure transducer

### 4.2.1 Manufacturing the 1/4 Scale Rear Wing

Blueprints | FiXme Note: Why this

wing design? answer: Just
a first guess that can be
compared with easily
later.

The small scale rear wing is constructed in 6 pieces. The large wing is dissected into three parts. Two regular wings, and a central part with 15 pressure taps.

Material selection is based on the ease of machinability - a CNC-miller was provided to us, along with ample amounts of aluminium. This scale wing is not to be used in the actual race car, so weight is not a concern.
Construction the 1/4 scale wing is not completely trivial. High precision
is required for the surface finish, and the pressure taps have to be small
in diameter: 0.8 mm. . | FiXme Note: insert work drawings used for producing the wing FiXme Note: Insert Technical Drawings

Tolerances

FiXme Note: Maybe
remove this section

Manufactured parts

In figure 4.1 the down-scaled wing post-production with pressure tubes inserted can be seen with pressure-taps along the centerpiece.

4.3. Experimental Procedure

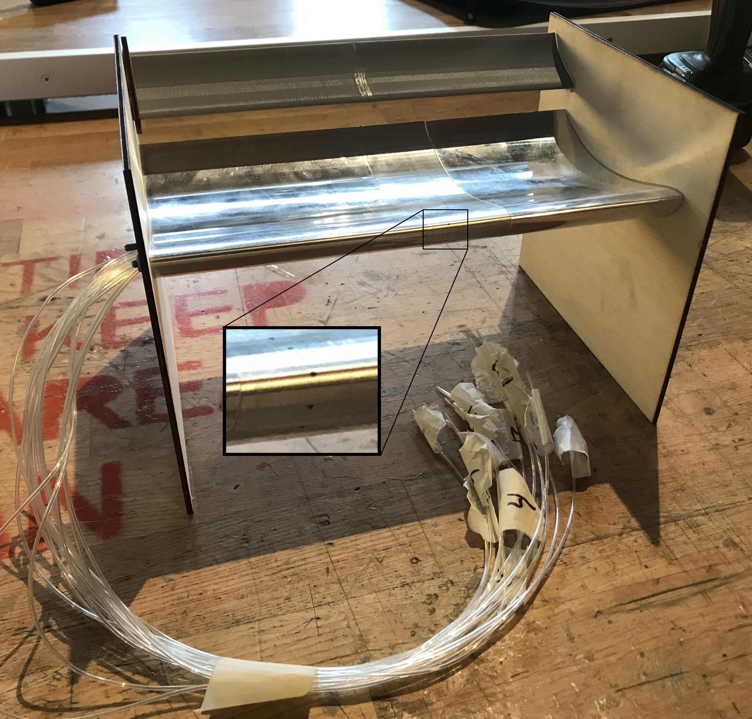
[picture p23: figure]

Figure 4.1: Down-scaled wing assmembled with a zoom in on the pressure taps. The length of the entire wing is approximately 250 mm with a total chord length of 150 mm.

### 4.3 Experimental Procedure

Given the nature of the competition, the average cornering speeds are around 55 km h⁻¹ = 15.28 m s⁻¹
, which is where downforce is of most importance. As shown in section 4.1.1, the desired velocity in the wind tunnel for the scale model can be found from equation 4.5

um =

0.6 m
0.15 m15.28 m s⁻¹ = 61.12 m s⁻¹

Which in accordance to the range of The Red wind tunnel.

### 4.4 Results

5

# Simulation

The simulation will run in several parts. First, the wings relative placement between eachother will be optimized in a 2-dimensional environment. This involves, size, x- and y-distance between the multi-element wings, angle of attack and height relative to the chassis to give a good estimate of the wings placement range. Secondly, a 3-dimensional analysis of the entire wing with endplates will be performed. Endplate dimensions will be optimized, and further optimization of the height relative to the entire chassis to finalize the design and placement. Lastly, a complete computational solution to the entire car will finalize the aerodynamical package, and yield the total amount of drag and downforce.

### 5.1 Star-CCM+

### 5.2 Finite Volume method

Star-CCM+ employs the finite volume method, which will be covered briefly in this report.

### 5.3 Mesh Generation

The mesh has to be structured in accordance to best practice. Areas with high velocity and pressure gradiants have to be dissolved in acceptable resolutions, in order to ensure correct results. Running an initial test on a generic mesh shows us where the wing requires greater resolution. Gradiants are easily visible around the wing’s leading edge, and generally
around the solid bodies. Furthermore, aligning the meshg with the flow
improves accuracy and rate of convergence. . | FiXme Note: Noget med konvergens undersøgelse. Måske også grid sensitivity test.

5.4. The Rear Wing

### 5.4 The Rear Wing

### 5.4.1 Verification of Simulation Results

Comparison with wind tunnel test.

Evaluation of Verification Simulation

### 5.4.2 Multi-Element Wing Optimization

Wing was moved around to optimize lift. Here’s the results changing the variables.

### 5.5 The Aerodynamics Package

### 5.5.1 Undertray, Diffuser, Front Wing and Driver

### 5.5.2 Everything Together Now

### 5.6 Results

6

# Construction

In order to verify the computational fluid dynamics used, a 1/4 scale wing was constructed. This miniature wing is constructed for performing windtunnel tests, and comparing results with the simulations. If the two are in accordance, the simulated results of the full scale wing can be used with confidence.

### 6.1 Requirements

FiXme Note: Dimensional
requirements from the
competition. Show CAD
of car-design.
Requirements to strength

### 6.2 Prototyping

### 6.3 Material Selection

FiXme Note: Overvej CES

### (for flair jo) 6.4 Composites

### 6.4.1 Sandwich Structure

### 6.4.2 Wing Deflection

### 6.5 Final Design of Rear Wing

FiXme Note: Presentation
of CAD Drawings and
method of how we will
get to this result
FiXme Note: Rendering

### 6.5.1 Blue Prints

### 6.6 Manufacturing Final Design

### 6.6.1 Polystyrene Molds

The molds for the wings were chosen as positive molds, meaning polystyrene molds of the actual wings were cut out and overlaid with resin coated car-

6.6. Manufacturing Final Design

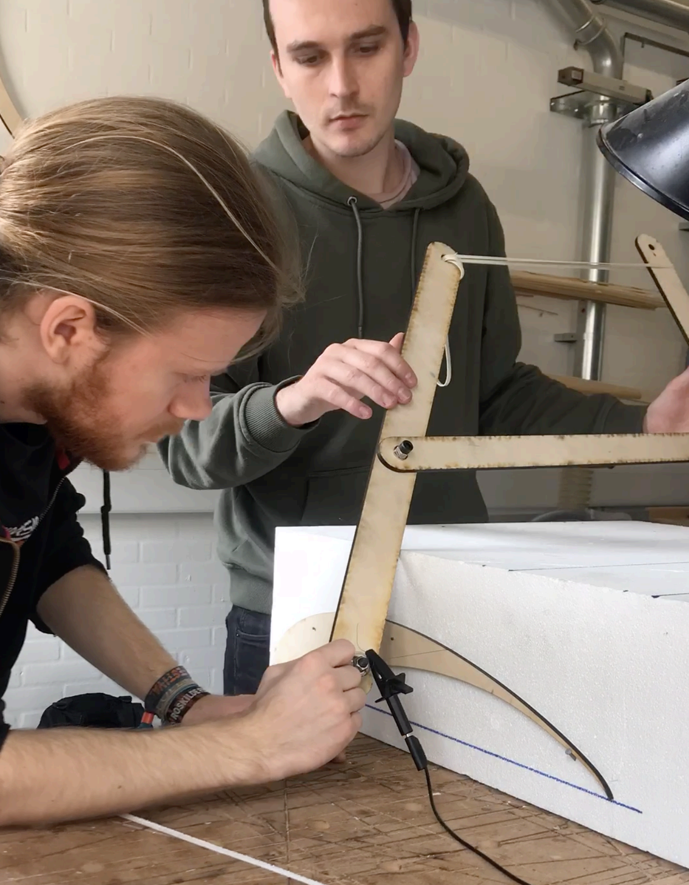
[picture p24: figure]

Figure 6.1: The hot wire melts the styrofoam while sliding along the wooden template.

bon fiber. In order to do this, we devised a hotwire-based specialized tool for the job. This can be seen in figure 6.1, and the name of the job is to do it slowly in order to receive a clean surface.

6.7. Testing and Inspection
6.6.2 Hand Layup | FiXme Note: Show how
| we did the hand lay up. What went wrong what went well.

### 6.6.3 Surface Finish

### 6.6.4 Implementation and Testing

### 6.7 Testing and Inspection

### 6.7.1 Reinforcing the mounting

7

# Discussion

8

# Conclusion

bla

# Perspective

The Eevee has to be rebuilt next year, and in order to help the effort along for future students, a list of potential upgrades are listed below, with estimates of how valuable each change is in regards to downforce/drag reduction gain.

### 8.1 Drag Reductive System

A drag reductive system (DRS) is well-known from Formula 1, and has in the recent years been gaining traction (or lack therof :))) ) in the Formula Student. It is a natural extension to the aerodynamics of the car, as Formula Student has much less restrictions on aerodynamics than Formula 1. Automatically adaptive DRS, that measures the car’s relative downforce and the angle of the steering column could give a big edge on straights, as flipping the wing up to reduce drag increases the top speed.

### 8.2 Slats, Flaps, Gills and Cutaway

https://www.jmranalytical.com/single-post/2017/04/06/Rear-Wing-Investigation

We already have a multi element wing, but increasing the amount of elements increases the amount of downforce we can pull out of the same design.

### 8.3 Suspension Integration

- Nice to have downforce directly on the wheels - Gives more unsprung mass though. That might be an issue.

# Bibliography

[1] Bulbapedia. http://bulbapedia.bulbagarden.net/wiki/Eevee,
may 2016.
[2] Joseph Katz. Race Car Aerodynamics. BentleyPublishers, 2nd edition, 2003.
[3] J.R. Taylor. Classical Mechanics. University Science Books, 2005.
[4] IMechE: Institution of Mechanical Engineers. Formula Student Rules. 2018.
[5] lcdesign. Formula sae aerodynamics. https://sites.google.com/

site/lcdesignwork/case-studies/automotive-case-studies/ formula-sae. (https://sites.google.com/site/lcdesignwork/case-studies/automotive-case-studies/formula-sae)

[6] HPWizard. Tire friction and rolling resistance coefficients. http://
hpwizard.com/tire-friction-coefficient.html.
[7] George P. Sutton and Oscar Biblarz. Rocket Propulsion Elements. Wiley, 8th edition, 2010.
[8] John D. Clark. Ignition!: An informal history of liquid rocket propellants. Rutgers University Press, 1st edition, 1972.
[9] Seppo A. Korpela. Principles of Turbomachinery. Wiley, 1st edition, 2012.
[10] James G. Quintiere. Principles of Fire Behaviour. Delmar, 1st edition, 1997.
[11] Julio de Paula Peter Atkins. Atkin’s Physical Chemistry. Oxford University Press, 10th edition, 2014.
[12] Nancy Hall. Compressible Area Ratio. https://www.grc.nasa.gov/
www/k-12/airplane/astar.html, (https://www.grc.nasa.gov/www/k-12/airplane/astar.html) May, 2015.

Bibliography

[13] Nancy Hall. Isentropic Flow. https://www.grc.nasa.gov/www/
k-12/airplane/isentrop.html, (https://www.grc.nasa.gov/www/k-12/airplane/isentrop.html) May, 2015.
[14] SierraPine. MDF Material safety data sheet, January 2005.
[15] Thermocouples: Using Thermocouples to Measure Temperature.
http://www.omega.com/prodinfo/thermocouples.html, 2016.
[16] Richard Nakka. Propellant Grain. http://www.nakka-rocketry.
net/th_grain.html, (http://www.nakka-rocketry.net/th_grain.html) july 2001.
[17] Richard Nakka. Nozzle Theory. http://www.nakka-rocketry.net/
th_nozz.html, (http://www.nakka-rocketry.net/th_nozz.html) April 2014.
[18] Robert A. Braeunig. | Nozzle. | http://www.braeunig.us/space/
propuls.htm, (http://www.braeunig.us/space/propuls.htm) 2012.
[19] E659-78. Standard test method for autoignition temperature of chemicals. ASTM, 14(5), 2000.
[20] Anders Hjort-Degenkolv Kristensen Alex Nørgaard, Martin Gosvig Jensen. Undersøgelse af regressionsrater i en hybrid raketmotor, 2015.
[21] HorsePunchKid. De laval nozzle. https://en.wikipedia.org/wiki/
Rocket_engine_nozzle#/media/File:De_laval_nozzle.svg. (https://en.wikipedia.org/wiki/Rocket_engine_nozzle#/media/File:De_laval_nozzle.svg)
[22] Philip-J. Pritchard Robert W. Fox, Alan T. McDonald. Introduction to Fluid Mechanics. Wiley, 6th edition.
[23] Frank M. White. Fluid Mechanics. McGraw-Hill Higher Education, 4th edition.
[24] Steven S. Zumdahl. Chemistry. Houghton Mifflin, 7th edition.
[25] Enthalpy. http://fchart.com/ees/eeshelp/eeshelp.htm.
[26] Merle C. Potter. Mechanics of Fluids. Cengage Learning, 4th edition.
[27] Industrial Measurements Systems Inc IMS. http://imsysinc.com/
Knowledgebase/ultratherm.htm. (http://imsysinc.com/Knowledgebase/ultratherm.htm)
[28] The Engineering ToolBox. Wood-combustion heat.

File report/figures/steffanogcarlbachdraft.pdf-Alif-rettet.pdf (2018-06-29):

# Aerodynamic design, simulation and test of rear wing for a Formula SAE


# race car

## written by

### Carl-Emil Grøn Christensen, s170817

Steffan Johan Kirk, | s170816

## Supervisor

### Jens Honoré Walther

Department of Mechanical Enginering, DTU
In fulfillment of the requirements for the degree of Bachelor of Science in Mechanichal Engineering

# Preface

This bachelor thesis was prepared at the department of Mechanical Engineering at the technical University of Denmark in fulfillment of the requirements for acquiring a Bachelor of Science degree in Mechanical Engineering. This bachelor thesis represents the work of 2 × 15 ECTS points. The work in this thesis is considered evenly distributed between both students.
The entire project is publicly available on https://github.com/carlegroen/bachelor_project_racecar_aero, (https://github.com/carlegroen/bachelor_project_racecar_aero) where all work files, data, various notes and CAD drawings can be found.

Carl-Emil Gr!n Christensen (S170817) Date

Steffan Johan Kirk (S170816) | Date

iii

# Acknowledgements

We would like to thank our supervisors Jens Walther and Robert Mikkelsen, who allowed us to learn intricate details about our own personal project. A special thanks to everyone on the team of Vermilion Racing, who in less than a year managed to take a dream and make it reality. Vermilion Racing is going to compete at the Silverstone race track the 10th of July, where all of our ideas and designs are going to be tested to the limit.
The sponsors who made this project possible are all found on the following page. A big thanks goes out to everyone who supported us and assisted us in creating this project.
Thanks to Rasmus Himborg from Philips Lighting Denmark, for helping us machine a 1/4 scale wing used in the wind tunnel tests.
Thanks to Daniel Rasmussen, Bo Tranberg and Jacob Buch for assisting with graphical setup of the report and making sure our figures are beautiful.
Thanks to Nicolai Boertmann and Daniel Rasmussen for the help building the composite wings.
Thanks to DTU Skylab, and especially Martin Meister, Rasmus Bruun, Ralle Malone and Tonja Kramer for always having the time to help us when things looked most dire.
Lastly, a thank to Nenad Mijatovic. Nenad is the overall supervisor for Vermilion Racing and is a significant reason we recently became a DTU Blue Dot project - a highly prestigious title that will ensure that the team will survive for many years to come.

v

Karl Pedersen & Hustru Fond Mogens Balslevs Fond

JD Design APS

vi

## Abstract

The ability to aerodynamically improve grip without adding a weight penalty is key to winning with race cars. High downforce is highly sought after, and the newly started Vermilion Racing at DTU is no exception. This work presents the theoretical arguments showing why downforce is important and numerical simulations to optimize the proposed wing dimensions. The numerical simulations are held up against a wind tunnel experiment, showing how misalignment of wings can greatly interfere with airflows, confirming the complexity of designing aerodynamical parts. The results is the design specifications of an easily producable rear wing with two elements and large end plates, providing an improvement in cornering speeds between 3 − 45%, depending on the turn radius.

vii

# Nomenclature

α | Angle of attack
α0 | Effective angle of attack due to airfoil camber
A | The effective aspect ratio of the wing
Aactual The actual aspect ratio of the wing
x# | Acceleration in x-direction
x# | Velocity in x-direction
ϵ | Wing tip geometry constant
µ | Friction coefficient
ν | Kinematic viscosity
ρ | Fluid Density
Eu | Eulers number
Re | Reynolds number
A | Frontal area or planform area
b | width of the wing
c | Chord length
CD | Total drag force
Cd | Drag coefficient of air resistance
CL | Lift coefficient
Cl | Lift coefficient for 2D airfoils
| ix

Cdinduced Drag coefficient of induced drag

FiXme Note: fix this CLα | DONT KNOW HELP
E | Young’s Modulus
Fcentripetal Centripetal force Ffriction Force due to friction Fnormal Normal force
Fd | Drag force
FL | Lift force
fl | Lift force per unit width
Fx | Sum of forces in x direction
g | Force due to gravity
h | Height of end plate
I | Second moment of inertia
L | Characteristic length of item
Lm | Characteristic length of model
m | Mass
P | Motor effect
r | Turn radius
u∞ | Velocity of fluid
um | Fluid velocity of model
x | x-position
AOA Angle of Attack
CM Center of Mass
PDS Product Design Specification

x

# Contents

1 Introduction | 1
2 Aerodynamic Effects on Vehicle Performance | 5
3 Airfoils and Inverted Wings | 9
4 Concept Design | 17
5 Wind Tunnel Experiment | 23
6 Simulation | 33
7 Construction | 39

xii

8 Discussion | 49
9 Conclusion | 53
A Appendix | 59
B Carbon Fiber Data Sheet | 61
C Hardener Data Sheet | 63
D Resin Data Sheet | 65
Bibliography | 67

xiii

1

# Introduction

Vermilion Racing is a newly started Electric race car team building their first vehicle: The Eevee [1]. The teams’ purpose is competing against other Universities at the Silverstone race track from the 11th to the 16th. As members of the team, the purpose of this report is to document the design process of the rear wing of the first car, the Eevee, and provide an aerodynamic package documenting drag and downforce, thereby allowing the work to be passed on to following students on


Figure 1.1: The teams’ race car with the conceptual design of the rear wing.

1

1. Introduction

the team. A render of the car’s design as of the 31st of June is shown in figure 1.1. As this is the first car, this project sets out to uncover the requirements, theory and know-how behind building a rear wing.
Aerodynamics is a major decider in racing today. Cornering, not top speed is the deciding factor amongst the teams, and aerodynamics is the key. Drag, lift and side force are the three cornerstones to vehicle aerodynamics. A car’s ability to handle depends on the grip of the tyres, and downforce directly increases grip by increasing the downwards load on the tyres without adding a weight penalty. Additionally, drag directly decreases the speed of a vehicle by increasing air resistance, but is of less importance as the car’s in this class have far more accelerative power than the tyres can handle [2]. Designing the bodyworks of Eevee is therefore a dance of downforce.
This bachelor thesis attempts to lay down the ground work for designing, optimizing and manufacturing the car’s rear wing. Our advisor, Jens Honore Walther, proposed simulating the wing geometry in order to both cheapen and quicken the optimization process, but also gain insight into how flow in front of the rear wing affects lift performance. The purpose of the numerical simulations are ultimately to create an easily producable wing in a very short timespan, that FiXme Note: write about produces ample amounts of negative lift for the time spent in production. what has been done prior As this is the first year the team is designing and building a car, time and money for production is sparse. To ensure the simulated optimizations are true, a wind tunnel test is performed on a down-scaled wing using Flow Similarity theory. The measurements are compared with the results from a computational fluid dynamics simulation performed in Star-CCM+ to verify the preciseness of the simulations. Based on this, the size, x- and y-distance between the multi-element wings, angle of attack and height relative to the chassis is then optimized for maximum downforce. The multi-element wing is taken from theoretical abstraction to reality with a physical design of the wing. The position, deflection and dimensions of the wing is thoroughly described by the rules of the Formula Student competition, guiding the final design process. In the final chapter, theories regarding strength of sandwich structured composites and carbon fiber molding are handled, in order to descibe the production choices made. Finally, the end result is discussed and possible improvements to the wing and mounting system is listed.
Measurements and tests have been carried out at the DTU Wind laboratory’s Red wind tunnel with the help of our supervisor Robert Flemming Mikkelsen the 19th and 20th of June.

2

1.1. Design Philosophy

The entire project is publicly available on https://github.com/carlegroen/bachelor_project_racecar_aero, (https://github.com/carlegroen/bachelor_project_racecar_aero) where all work files, data, various notes and CAD drawings can be found. The Formula Student team at DTU: Vermilion Racing can be followed on fb.com/FSDTU.

## 1.1 Design Philosophy

Designing a car with hundreds, if not thousands of different factors is incredibly difficult. Therefore, determining which factors are most important for the cars performance very crucial to the teams’ success. First, the deadline for finishing the wing is short. This sets a limit on the complexity of the wing’s dimensions. Secondly, this is the first iteration of the car, thus no decision can be based on prior experience, and optimization has to wait for the next iteration. Finally, the finances for building the car are tight. This forces us to go with a low-cost solution. We therefore have to go for a simple, low cost wing, basing the design solely on litterature and experiences of the other competing teams.
The wing has to have as low weight as possible, in order to ensure optimum acceleration of the car. Thereto, drag has to be kept low, but the effect from drag is near negligible, which will be explained in section 2.1. Lastly, we have to maximize the downforce provided by the wing, but also ensure that the center of pressure is kept as constant as possible. If the frontwing, undertray and rear wing’s downforce don’t scale equally with speed, the center of pressure will move during acceleration. This will make the car’s handling unpredictable, and potentially limit the driver’s confidence in the car.

## 1.2 Problem Statement

A new aerodynamically beneficial structure is to be implemented at the rear of the Eevee, with the purpose of increasing the tyre’s grip without adding a weight penalty. The goal is to have a cheap, both time- and money-wise rear wing, which provides enough negative lift to benefit the car’s lap time.

3

2

# Aerodynamic Effects on Vehicle Performance

The first argument to the importance of aerodynamics is based around two facts: The fact that drag is neglible in regards to the Formula Student vehicle’s top speed on straights, and the fact that aerodynamically increasing the vehicle’s effective mass due to downforce increases tyre grip, which in turn allows for higher cornering velocities.
The second part of this chapter covers the importance of centering the effective mass increase due to aerodynamic devices close to the center of gravity – otherwise handling characteristics becomes a function of velocity.

## 2.1 Drag Effects on Straights

First, let’s explain what makes a car fast, and what parameters we can change to
improve the speed of our car.. The car’s acceleration can be described by Newton’s FiXme Note: introduce a
figure with drag and lift to show what’s going on

second law as:

FiXme Note: stort D eller
! | lille d i ligningen? Fx = ma | (2.1)

5

2.1. Drag Effects on Straights


Figure 2.1: Frontal area of the car with a dummy wing inserted into the CAD model, in order to get an estimate of the drag coefficient CD.

Where the sum of forces working in the x-direction (the direction of travel) can be expressed as the force already pertained by the vehicle: The force the motor exerts is given by F = P
x# , where P is the power of the car, minus the drag force: FD = 1
2

CD ρx#

2A | (2.2)

Fmotor = mx% = P
x# | (2.3)
!
Fx = Fmotor − FD = P
x# − CD

"
1
2

ρx#

2A

= 0 | (2.4)

Where CD is the drag coefficient of the vehicle, ρ is the density of the fluid it moves in and A is frontal area of the vehicle. Solving for maximum speed, that is, when the two forces sum to zero:

Fmotor = FD | (2.5)
As we were interested in the max speed of the car, let’s solve for the velocity, giving:

x# =

" 2P

CD (ρA)

1
3 | (2.6)

This is assuming we’re traveling at terminal velocity – that is, the point where the Driving Force = Friction Force. The terminal velocity of the racer is then easily calculated, as the competition restricts the maximum amount of power to 80 kW, and the frontal area of the car is approximated from the CAD drawing
FiXme Note: fix calculation seen in figure 2.1. to use 0.99 instead of 1.2
FiXme Note: missing
radiators
x#max =

" 2 · 80 kW
0.85 $
1.225 kg m⁻³ 0.9 m²

%

1
3
= 53.7 m s⁻¹ = 193.5 km h⁻¹ (2.7)

6

2.1. Drag Effects on Straights

however, given the ruleset a forecasted maximum of 110 km h⁻¹ allows a much larger drag coefficient CD:
CD = 2P

## x#³ (ρA)

= | 2 · 80 kW
(110 km h⁻¹

)³ $
1.225 kg m⁻³ 0.99 m²

% = 2.82 (2.8)

Thus, the car’s top speed will only be limited by a drag factor > 2.82, which is FiXme Note: insert source far above the drag introduced by the aerodynamic devices.
From this derivation, it is clear that the car’s abilities at maximum speeds far exceed
the requirement of the track. Therefore, the next step is to improve cornering
speeds which depend strongly on the tyre’s grip on the surface of the road [2].

### 2.1.1 Downforce Effects on Cornering

Shown before, drag does not limit the car’s performance on straights. During cornering, drag is not an issue either, but the grip of the tyres limits the maximum velocity before the vehicle loses traction due to the centripetal force which is given by: [3]
Fcentripetal = mx#²
r

(2.9)
wherer is the distance to the center of the cornering circle. The frictional force the car exerts due to downforce and tyre grip is given by:
Ffriction = µFnormal | (2.10)
where the normal force is given by both the weight and (negative) lift of the car, which serves as an effective mass increase:
FL = 1
2

CL ρAx#

2 | (2.11)

Ffriction = µ

"
mg +

1
2

CL ρAx#

2

(2.12)
The vehicle will lose traction when the frictional force is less than the centripetal force.
mx#²
r

>µ "
mg +

1
2

CL ρAx#

2

(2.13)
Giving the maximum velocity for a given corner radius before the car skids out:
⇒ x# <

" 2µmgr

m − µCL ρrA#
1
2
(2.14)
Again, the forecasted variation in radii of corners is prescribed by the rules to be between 3 m to 50 m [4]. Plotting this for various CL values between 1.5 to 2.6 [5], assuming m = 300 kg, µ = 1.5 [6] and A = 0.99 m² as previously used. The result can be seen in figure 2.2.

7

2.1. Drag Effects on Straights


Figure 2.2: Cornering speed as a function of turn radius for various lift coefficients.

### 2.1.2 Load Distribution

The scope of this thesis is not to incorperate a full aerodynamic package, but a quick overview of load distribution is essential to understanding the behaviour of the car.
The effective mass added from negative lift depends on the lift coefficient. It is evident that different items on the car carry different lift coefficients, thus making the lifting forces over the cars length a function of relative speed. For the unexperienced driver, this is not easily managed as handling characteristics change with velocity. Therefore, it is desirable to have the aerodynamic center of pressure close to the car’s center of gravity, in order to have similar handling at all velocities. While this is not handled in this thesis, it is ideal for future iterations and essential for a full aerodynamical package.

8

3

# Airfoils and Inverted Wings

FiXme Note: fix the dot x
Achieving a large negative lift coefficient C | to u for wind velocities L can be done in many ways. Inspect-
ing race cars throughout the years show that airfoils have been used as early as
1966 when Jim Hall attached a rear wing to his Chaparral 2E [7]. Since then,
the inverted wings have been a staple in the racing industry with various three
dimensional geometries affecting the overall performance even further.
This chapter covers the pressure distribution of various airfoils, the selection criterions of the competition, three dimensional geometrical effects and the tools of the optimization trade.
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

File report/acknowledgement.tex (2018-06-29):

% !TEX root = main.tex
\chapter*{Acknowledgements}

We would like to thank our supervisors Jens Honore Walther and Robert Flemming Mikkelsen, for giving us the opportunity to learn intricate details about our own personal project. A special thanks to everyone on the team of Vermilion Racing, who in less than a year managed to make a dream reality. Vermilion Racing is going to compete at the Silverstone race track the 10\textsuperscript{th} of July, where all of our ideas and designs are going to be tested to the limit.

The sponsors who made this project possible are all found on the following page. A big thanks goes out to everyone who supported us and assisted us in creating this project.

Thanks to Rasmus Himborg and Philips Lighting Denmark, for helping us machine a 1/4 scale wing used in the wind tunnel tests.

Thanks to Daniel Rasmussen, Bo Tranberg and Jacob Buch for assisting with graphical layout of the report.

Thanks to Nicolai Boertmann and Daniel Rasmussen for the help building the composite wings.

Thanks to DTU Skylab, and especially Martin Meister, Rasmus Bruun, Ralle Malone and Tonja Kramer for always having the time to help us when things looked most dire.

Lastly, a thank to Nenad Mijatovic. Nenad is the overall supervisor for Vermilion Racing and is a significant reason we recently became a DTU Blue Dot project - a highly prestigious title that will ensure that the team will survive for many years to come.
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

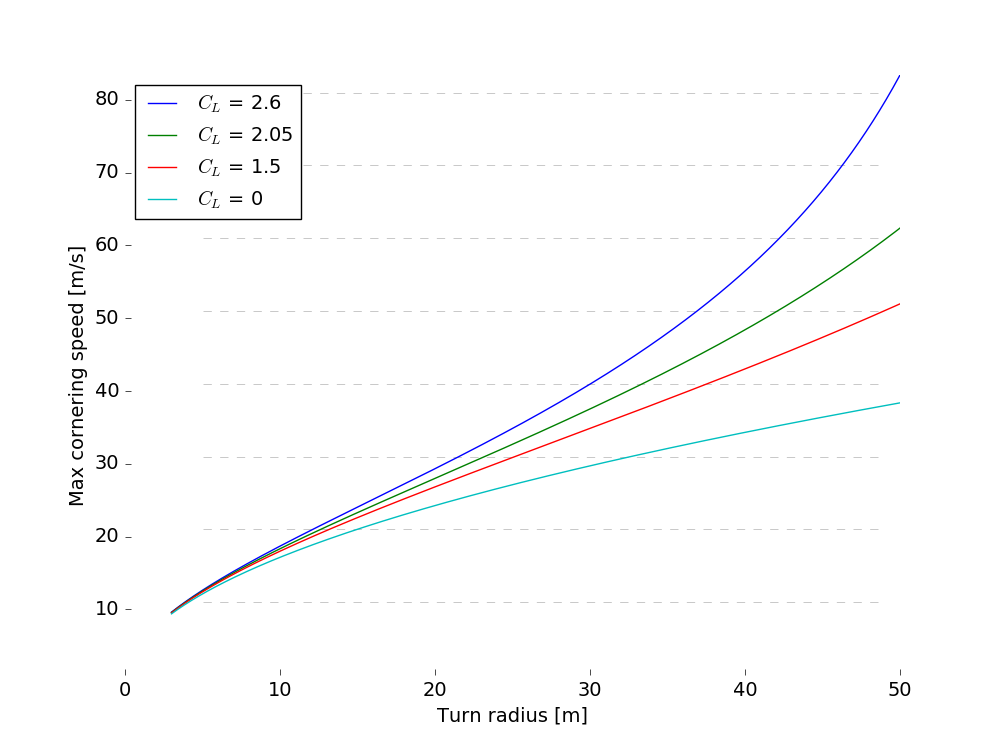
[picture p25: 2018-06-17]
report/figures/turnspeedperCL.png

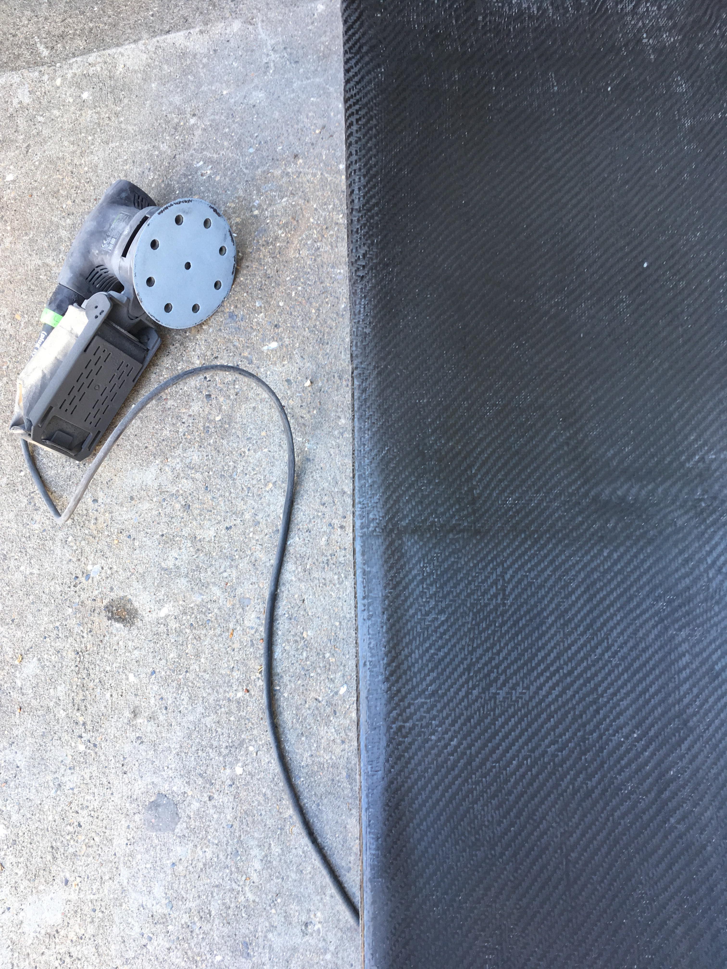
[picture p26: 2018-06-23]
report/figures/wingaftersanding.jpg

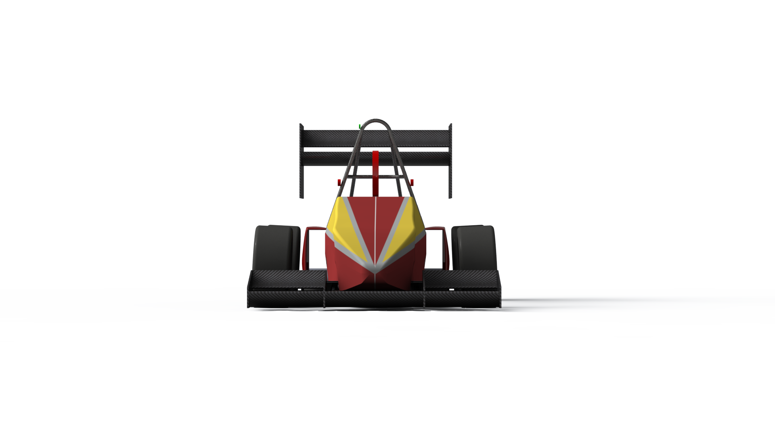
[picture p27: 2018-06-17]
report/figures/carfrontrender.png

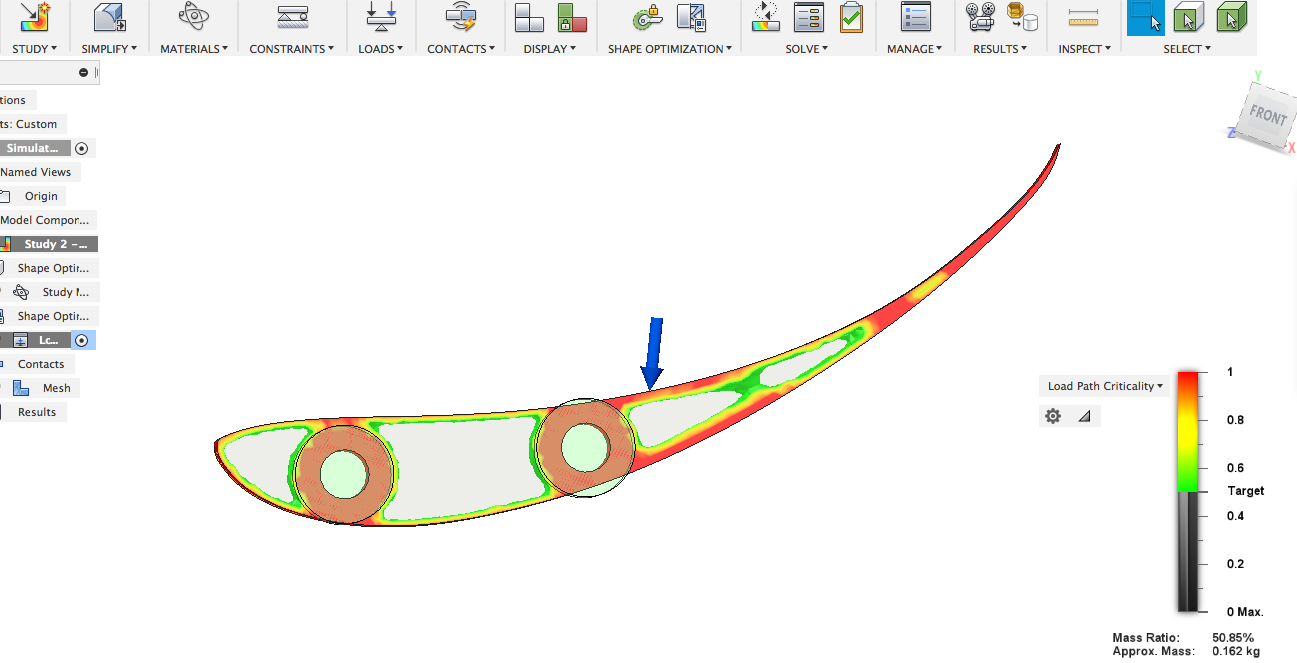
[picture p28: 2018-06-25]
report/figures/SmallInsertTopology.png

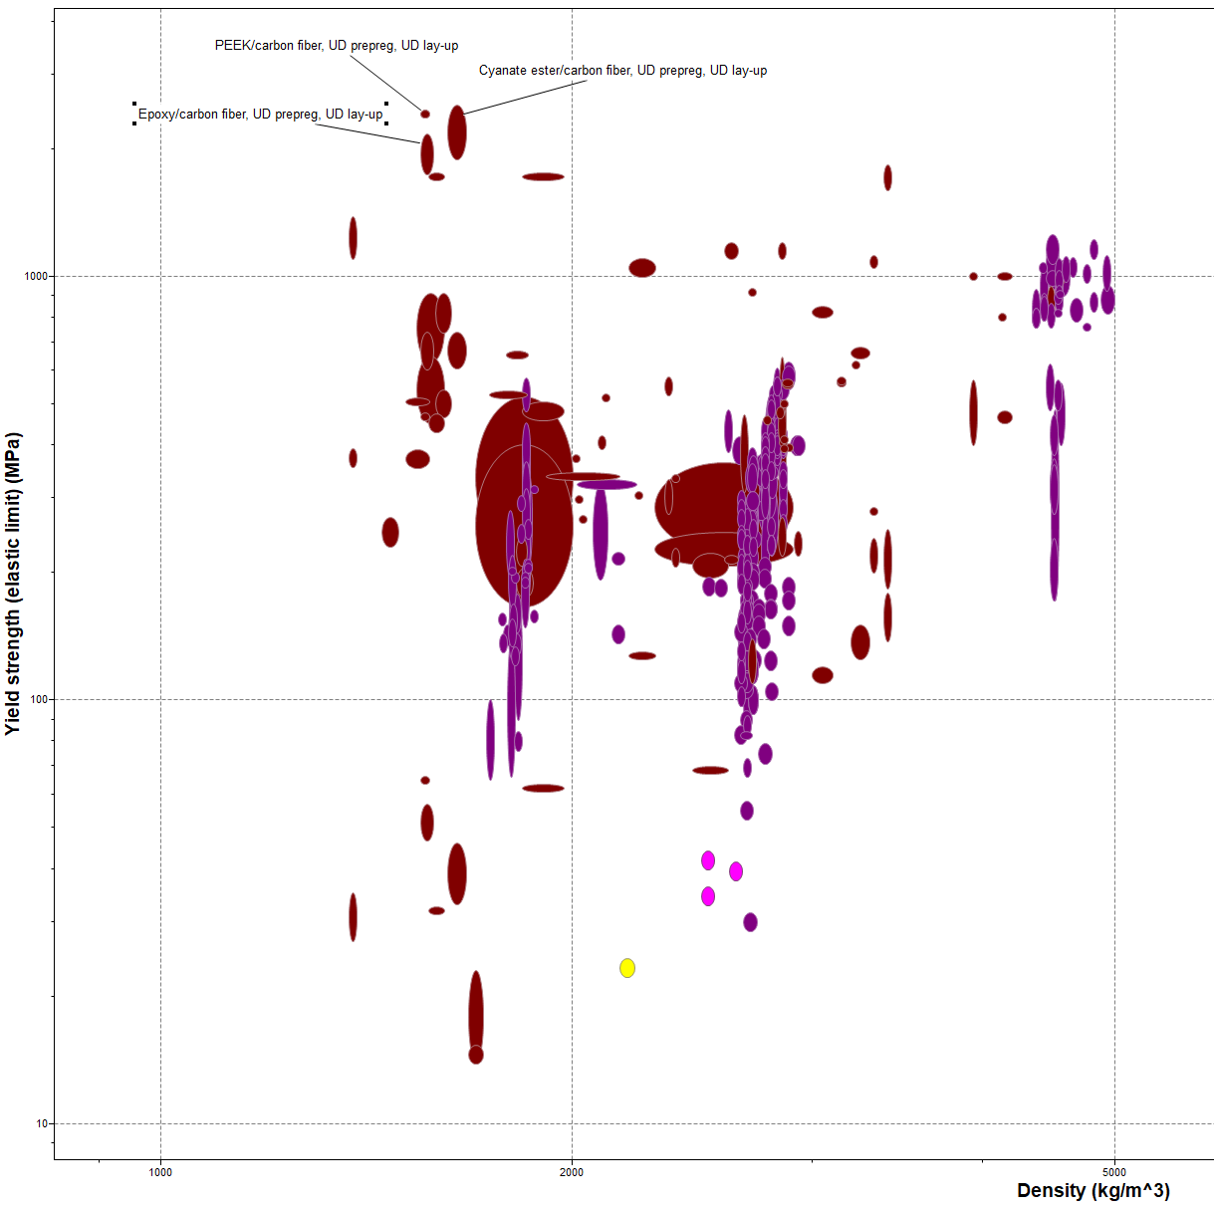
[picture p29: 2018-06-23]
report/figures/CESmatchoicebad.png

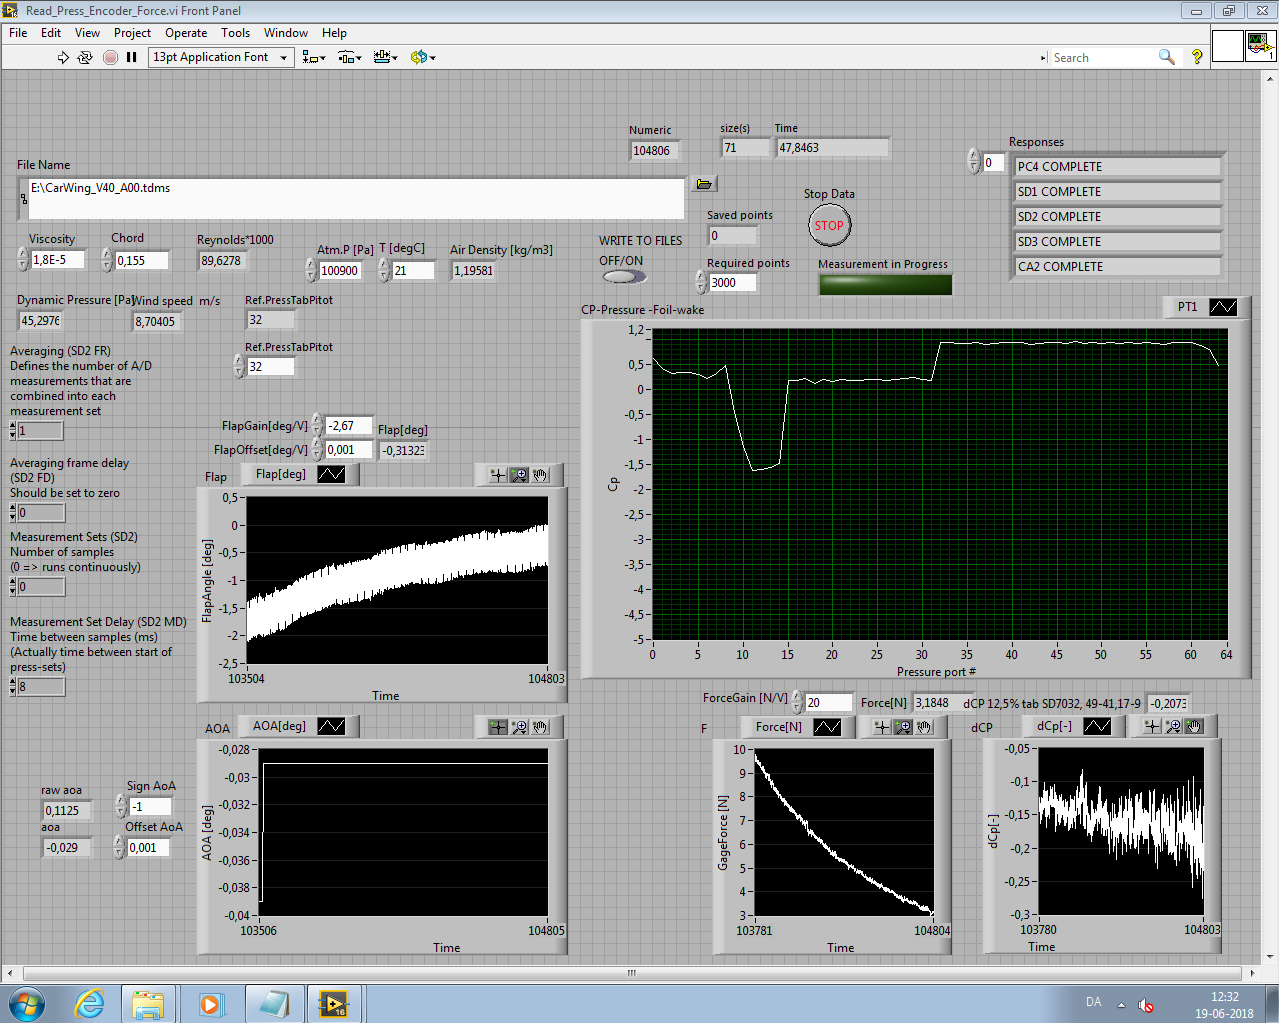
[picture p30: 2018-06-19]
report/figures/labviewview.PNG

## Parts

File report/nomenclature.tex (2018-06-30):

% !TEX root = main.tex

\nomenclature{$A$}{Frontal area or planform area}%
\nomenclature{$F_x$}{Sum of forces in $x$ direction}
\nomenclature{$m$}{Mass}
\nomenclature{$x$}{$x$-position}
\nomenclature{$\dot{x}$}{Velocity in $x$-direction}
\nomenclature{$\ddot{x}$}{Acceleration in $x$-direction}
\nomenclature{$C_d$}{Drag coefficient of air resistance}
\nomenclature{$\rho$}{Fluid Density}
\nomenclature{$P$}{Motor effect}
\nomenclature{$F_\text{centripetal}$}{Centripetal force}
\nomenclature{$F_\text{friction}$}{Force due to friction}
\nomenclature{$F_\text{normal}$}{Normal force}
\nomenclature{$\mu$}{Friction coefficient}
\nomenclature{$C_L$}{Lift coefficient}
\nomenclature{$C_l$}{Lift coefficient for 2D airfoils}
\nomenclature{$r$}{Turn radius}
\nomenclature{$g$}{Force due to gravity}
\nomenclature{$u_\infty$}{Velocity of fluid}
\nomenclature{$f_l$}{Lift force per unit width}
\nomenclature{$F_L$}{Lift force}%
\nomenclature{$L$}{Characteristic length of item}
\nomenclature{$\alpha$}{Angle of attack}
\nomenclature{AOA}{Angle of Attack}
\nomenclature{$\alpha_0$}{Effective angle of attack due to airfoil camber}
\nomenclature{$\AR$}{The effective aspect ratio of the wing}
\nomenclature{$F_d$}{Drag force}
\nomenclature{$C_{d_\text{induced}}$}{Drag coefficient of induced drag}
\nomenclature{$C_D$}{Total drag force}
\nomenclature{$\epsilon$}{Wing tip geometry constant}
\nomenclature{$\AR_\text{actual}$}{The actual aspect ratio of the wing}
\nomenclature{$h$}{Height of end plate}
\nomenclature{$b$}{width of the wing}
\nomenclature{$C_p$}{Pressure coefficient}
\nomenclature{$c$}{Chord length}
\nomenclature{PDS}{Product Design Specification}
\nomenclature{$\text{Re}$}{Reynolds number}
\nomenclature{$\text{Eu}$}{Euler number}
\nomenclature{$\nu$}{Kinematic viscosity}
\nomenclature{$u_m$}{Fluid velocity of model}
\nomenclature{$L_m$}{Characteristic length of model}
\nomenclature{$E$}{Young's Modulus}
\nomenclature{$I$}{Second moment of inertia}
\nomenclature{CM}{Center of Mass}
\nomenclature{$\delta_\text{max}$}{Maximum deflection distance}
\nomenclature{$E_{cs}$}{Young's modulus of composite shell}
\nomenclature{$E_c$}{Young's modulus of core}
\nomenclature{$E_f$}{Young's modulus of fiber}
\nomenclature{$E_m$}{Young's modulus of matrix}
\nomenclature{$\text{Vol}_{f\%}$}{Volume fraction of fiber}
\nomenclature{$E_\text{long}$}{Young's modulus along the direction of the fiber}
\nomenclature{$E_\text{transverse}$}{Young's modulus in the transverse direction}
\printnomenclature

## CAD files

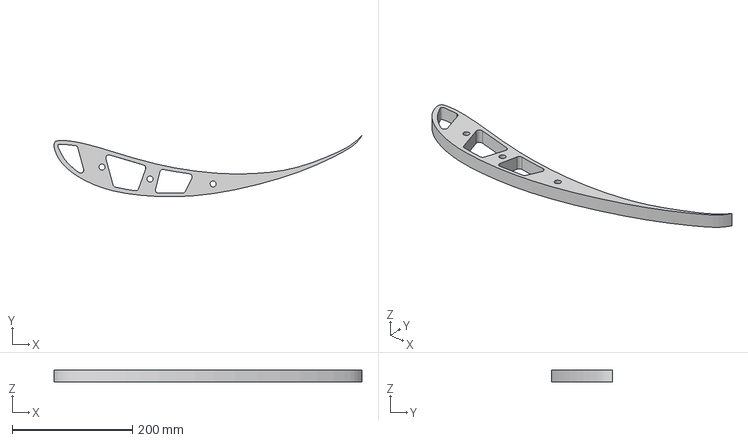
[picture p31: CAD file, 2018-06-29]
cad/MSHD double element v7 big insert.step
512.9 x 102.4 x 20.0 mm

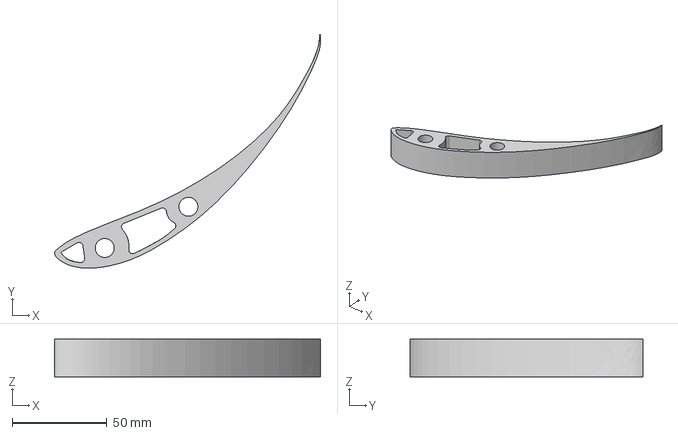
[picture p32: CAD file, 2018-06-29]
cad/MSHD double element small insert.step
140.6 x 123.3 x 20.0 mm

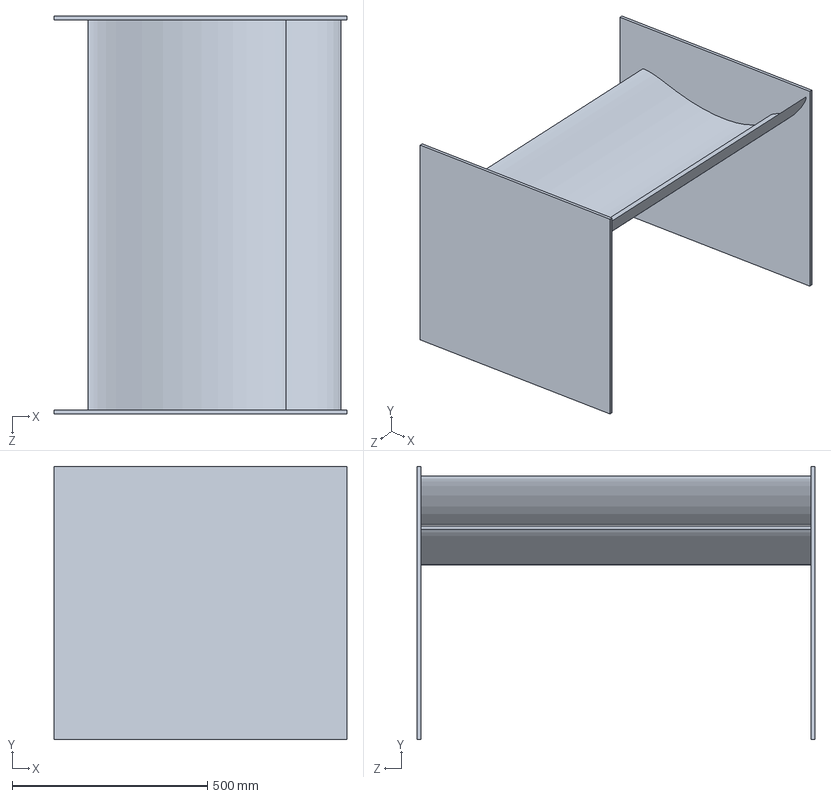
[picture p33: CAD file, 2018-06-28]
cad/MSHD double element optimized.SLDPRT
750.0 x 700.0 x 1020.0 mm

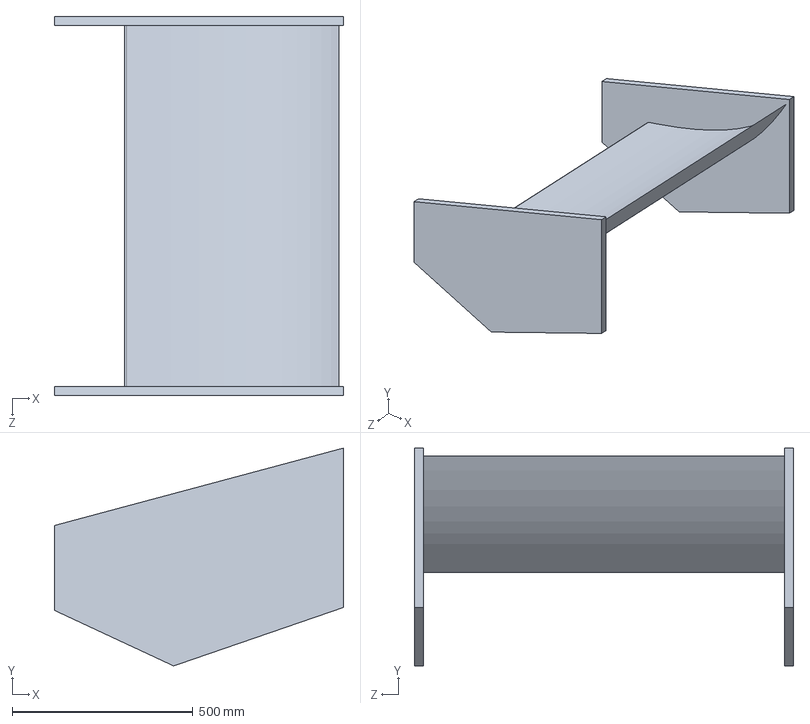
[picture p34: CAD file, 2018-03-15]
cad/airfoil test til starccm.SLDPRT
800.0 x 603.1 x 1050.0 mm

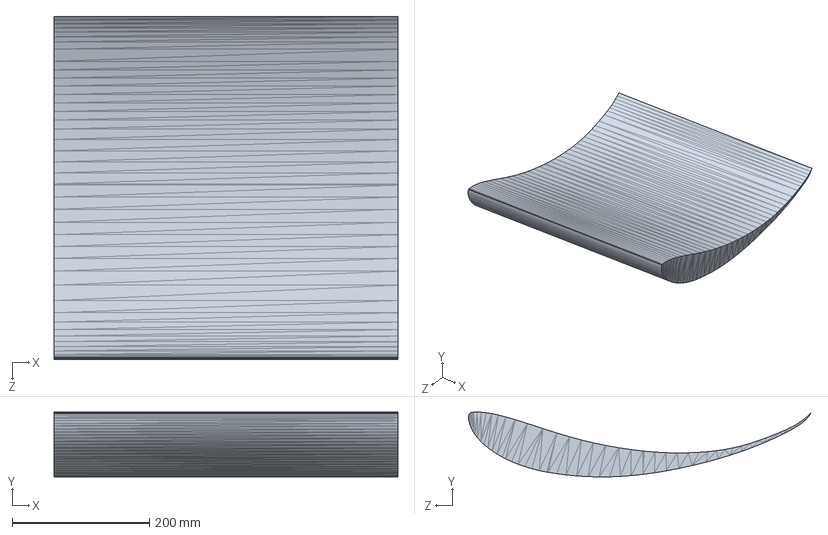
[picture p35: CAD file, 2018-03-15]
cad/MSHD_0st.SLDPRT
500.0 x 94.4 x 499.2 mm

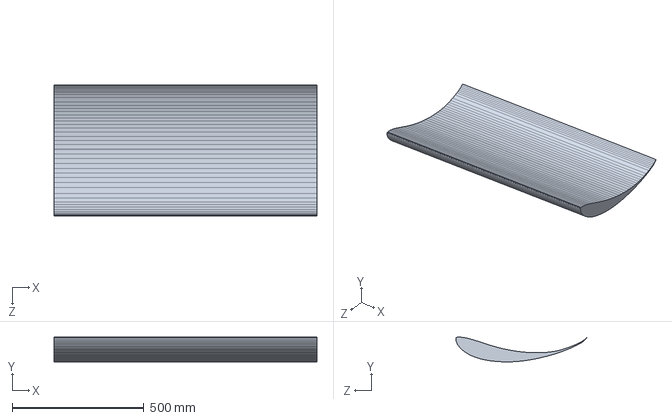
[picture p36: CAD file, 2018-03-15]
cad/MSHD.SLDPRT
1000.0 x 94.4 x 499.2 mm

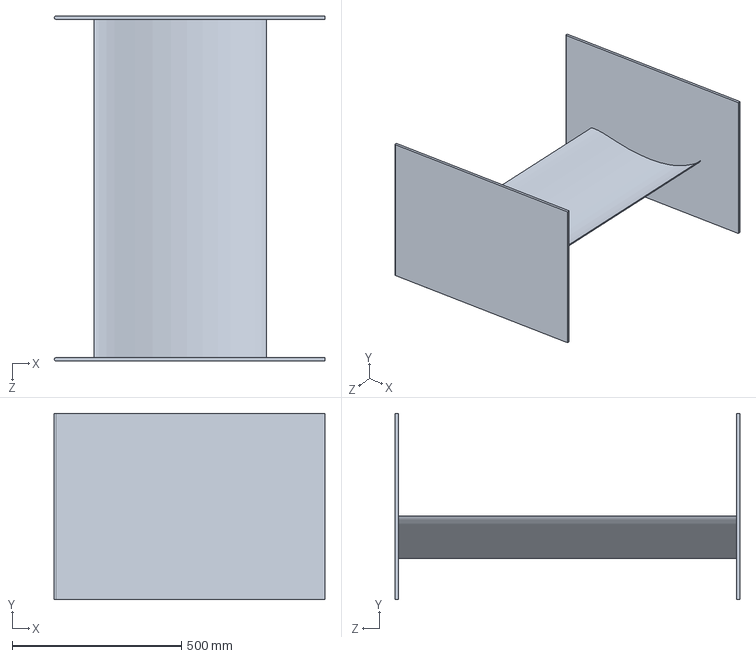
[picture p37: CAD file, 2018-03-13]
cad/MSHD Single element.SLDPRT
800.0 x 550.0 x 1020.0 mm

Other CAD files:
Presentation/Photos/laser vindtunnel.DWG
cad/MSHD double element.SLDPRT

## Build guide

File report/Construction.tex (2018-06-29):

% !TEX root = main.tex
\chapter{Construction}
\label{chap:construction}

  This chapter concerns the construction of the rear wing. The step from theoretical abstraction to a real product. This includes dimensioning, material selection and finalizing the wing. The simulated rear wing lacks a proper mounting method, as the design depends on the external group at Vermilion Racing.

\section{Requirements}

  The formula student competition has a clear ruleset dictating the strength requirements of aerodynamic devices. The most crucial elements are outlined below:

  \subsection{Strength Requirements}

    The competition rules set up strength requirements for the aerodynamic devices, making sure wobbling or unsafe structures are prohibited. The rules are seen below:

    \begin{tcolorbox}[colframe=seapurple,colback=seapurple!1]
      Aerodynamic Devices Stability and Strength:
      \begin{itemize}
        \item [T7.5.1] Any aerodynamic device must be able to withstand a force of $\SI{200}{\newton}$ distributed over a minimum surface of $\SI{225}{\centi\metre\squared}$ and not deflect more than $\SI{10}{\milli\metre}$ in the load carrying direction.
        \item [T7.5.2] Any aerodynamic device must be able to withstand a force of $\SI{50}{\newton}$ applied in any direction at any point and not deflect more than $\SI{25}{\milli\metre}$.
      \end{itemize}
      \vspace{5pt}
      \hspace*{\fill}\tiny{Rules from Formula Student UK 2018 ruleset \cite{FSrules18}.}
    \end{tcolorbox}

    Thus, deflection of the wing has to be calculated, in order to comply with the rules.

\section{Material Selection}

  Selecting a fitting material depends on the maximum deformation and weight. According to the PDS (see section \ref{sec:PDS}), the wing has to be \emph{as light as possible} in order not to move the center of mass further upwards. Furthermore, it needs a high \emph{elastic modulus} in order to be stiff as to not deform by aerodynamic forces. The wing needs to be have a \emph{high yield strength}, be \emph{low cost} and easy to produce time wise.

  Drawing on experience from competitors, carbon fiber- and glass fiber reinforced polymers are the weapons of choice \cite{FSwingmaterial}. However, Cambridge Engineering Selector, a material selection tool was used in order not to leave a stone unturned. The results can be seen in figure \ref{fig:CESmatchoice}, where materials of high elastic modulus are plotted against their density. Magnesium and some aluminium alloys are near the carbon fiber reinforced polymers, but machining an entire wing out of metal is incredibly time consuming and expensive. Carbon fiber reinforced polymers are chosen as a material, and the next chapter will investigate the properties and strength of the composite structure.

  \begin{figure}
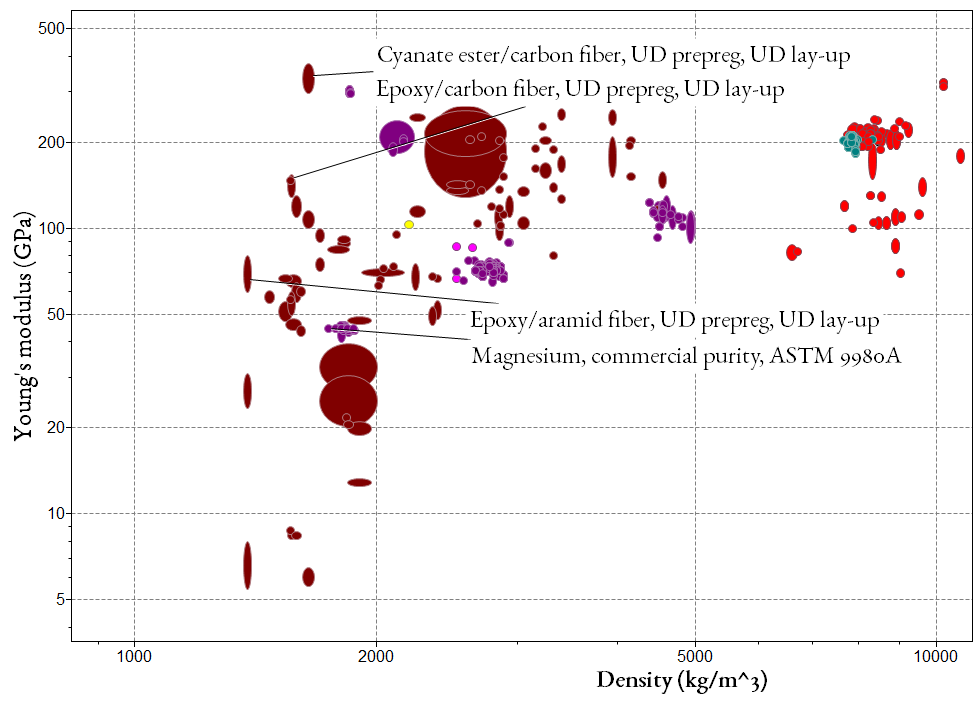
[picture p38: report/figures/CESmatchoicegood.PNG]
    \makebox[\textwidth][c]{}
    \caption{Cambridge Engineering Selector (CES) showing the various aerospace grade materials usable for this application. The dark red dots are composites, while the dark purple dots are metals such as aluminium and magnesium.}
    \label{fig:CESmatchoice}
  \end{figure}

\section{Composites}

  The geometrical shape of a composite structure can be highly varied, which can increase strength dramatically. The second moment of inertia of a simple beam can be increased by moving material from the neutral axis, as is done in a standard I-beam. The same thing applies to composites: A soft, but light core can be added with a hard shell (in this case carbon fiber) surrounding the core.

  An approximation of the wing profile is a box shape, where the moment of inertia is much easier calculated. From \cite{DIAB}, the strength of the sandwich material can be mathematically described as:
  \begin{align}
    D &= EI = E_{cs} \frac{bh^3 - ec^3}{12} + E_c \frac{ec^3}{12}
  \end{align}
  Where $E_cs$ is the elastic modulus of the composite shell, $E_c$ is the elastic modulus of the core, $b$ is the width of the beam, $h$ is the height of the beam, $e$ is the width of the core and $c$ is the height of the core.
  The strength of a fiber composite depends on the fiber direction, the relationship between the fiber and matrix, and the porosity of the composite. The load bearing properties in the fiber direction is given by:
  \begin{align}
    E_\text{long} &= E_f \text{Vol}_{f\%} + E_m (1-\text{Vol}_{f\%} )
    \intertext{Where $E_f$ is the elastic module of the fiber and $E_m$ is the elastic modulus of the matrix. The $\text{Vol}_{f\%}$ is the fiber volume fraction of the composite. For a transverse load, which is what rule T7.5.1 and T7.5.2, the strength of the sandwich construction is found as:}
    \frac{1}{E_\text{transverse}} &= \frac{\text{Vol}_{f\%}}{E_f} + \left( 1 - \frac{\text{Vol}_{f\%}}{E_m}\right)
  \end{align}
  For the biaxial carbon fiber weave used in this construction, the strength is almost $50\%$ less in the transverse direction \cite{DIAB}. The effective elastic modulus is found to be $\approx \SI{60}{\giga\pascal}$. Using the beam approximation that the deflection of the rear wing functions as a beam with a core supported in both ends is found to be: \cite{tekniskstabi}

  \begin{align}
    \delta_\text{max} &= \frac{PL^3}{192EI} = \SI{0.03}{\milli\metre}
  \end{align}

  Which is far below the maximum allowed by a factor of more than $300$. This also ensures the wing keeps its dimensions even though a high downforce is present.

\section{Final Design of Rear Wing}

\begin{figure}
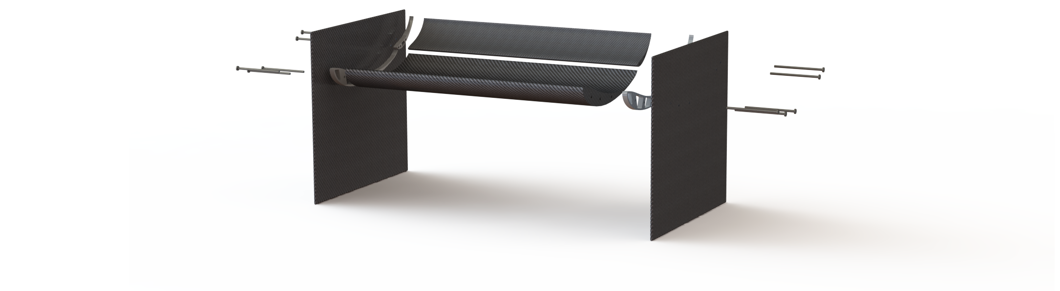
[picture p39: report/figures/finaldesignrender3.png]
  \makebox[\textwidth][c]{}
  \caption{Render of the final design of the rear wing in exploded view.}
  \label{fig:finaldesignrender}
\end{figure}

  Designing the final design can be done based on the investigations produced in the previous chapters. First, the FSUK rules restrict the cross sectional dimensions, as seen in figure \ref{fig:cadplacement}. Thereto, the rule \emph{T7.3.2   All aerodynamic devices higher than 500 mm from the ground, must not extend outboard of the most inboard point of the rear wheel/tire} dictates the width of the wing. According to the car's current design, the inner dimension from wheel to wheel is $\SI{1100}{\milli\metre}$, and thus serves as the maximum width of the wing.

  The two elements of the full scale wing will be bolted to the endplates at the optimal found angle of attack. The wing elements will have two metal brackets glued to the inside of the carbon fiber wings, the bracket will be have holes with M10 threads in which the endplates are bolted to secure the structure. The structure can be seen in figure \ref{fig:finaldesignrender}, with end plates, brackets, wings and bolts.

  \subsection{Topology Optimization of Wing Brackets}

  In order to minimise the weight of the metal bracket inserts topology optimizations where made using the build in function in \emph{Fusion 360}, in which all simulations are done in the cloud. Topology optimization tries to reduce the weight of the model by removing excess material while maintaining stiffness and strength of the model.

  The inserts were modelled from the wing profile and the location of the inner threads was chosen. The model was then meshed with a target cell size of $\SI{1.5}{\milli\metre}$, and the target weight reduction was set to $70\%$, with a downforce load of $\SI{250}{\newton}$ at the surface.

  \begin{figure}
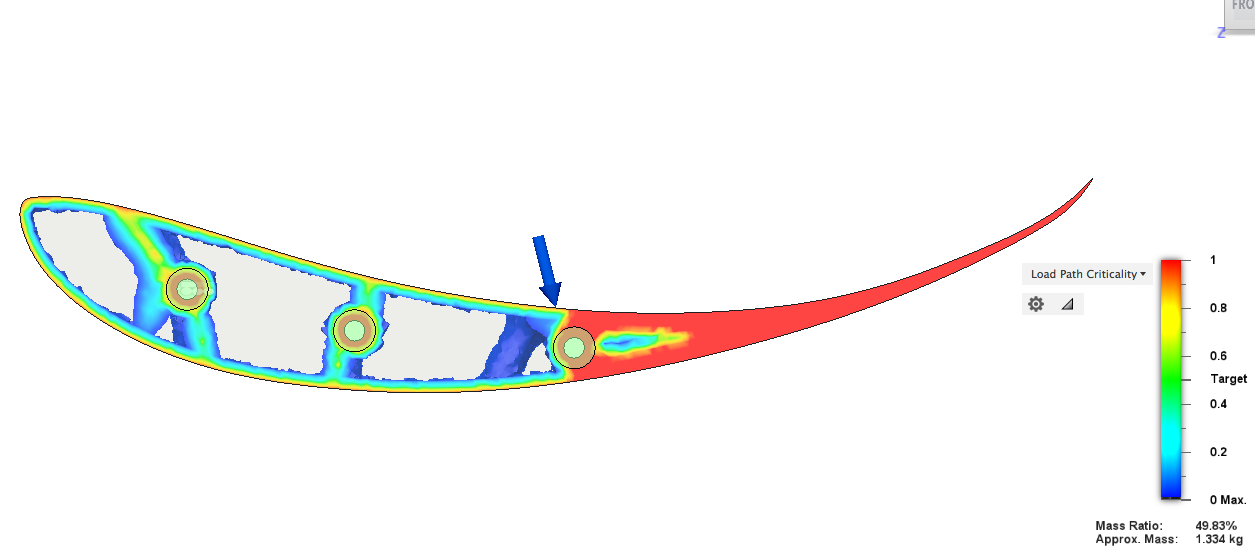
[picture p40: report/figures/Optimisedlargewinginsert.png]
    
    \caption{The result of the topology optimization for the large insert, with a weight reduction at about $\SI{50}{\%}$.}
    \label{fig:topology_large_insert}
  \end{figure}

  The result of the optimization for the large insert is shown in figure \ref{fig:topology_large_insert}, was then used to remove excess material from the model. The results were overlaid on the model and material could be cut from the original model as shown in figure
  \ref{fig:meshoverlay}. The final model of the large insert was then created with a weight reduction around $\SI{40}{\%}$. A render of the final model is shown in
  figure \ref{fig:render_large_insert}. The same procedure was done for the smaller metal wing insert, and technical drawings of are included in the online appendix \url{https://bit.ly/2tQXmkX}.

  \begin{figure}
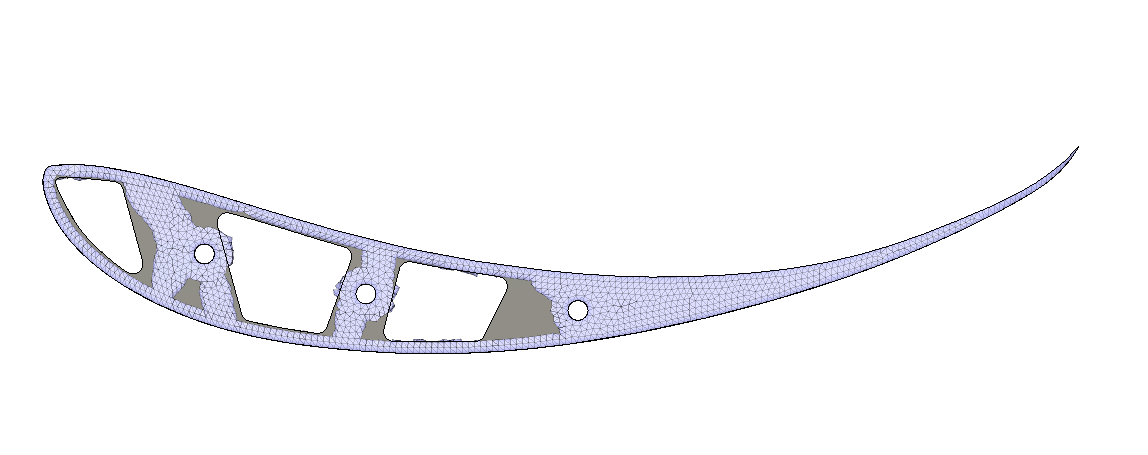
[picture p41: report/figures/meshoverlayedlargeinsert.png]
    
    \caption{Optimized mesh overlayed on model so excess material could be easily removed.}
    \label{fig:meshoverlay}
  \end{figure}

  \begin{figure}
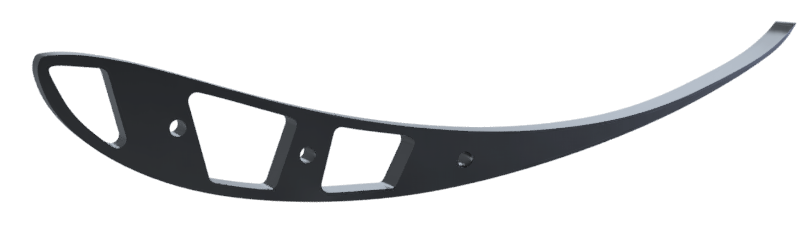
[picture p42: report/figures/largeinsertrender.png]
    
    \caption{Render of the final model for the metal insert, with a weight reduction around $\SI{40}{\%}$.}
    \label{fig:render_large_insert}
  \end{figure}

  The two elements of the full scale wing will be bolted to the end plates at optimal found angle of attack. The wing elements will have two metal brackets glued to the inside of the carbon fiber, the bracket will be have holes with M10 threads in which the endplates are bolted to secure the structure.

\section{Manufacturing Final Design}

  The following section describes the steps required to build the wing physically. First, templates of the MSHD airfoil are lasercut. The templates are mounted on the sides of polystyrene blocks, where a homemade hot wire cutter cuts the foam cores of the wing. The foam cores are then glued together into the appropriate lengths, where the carbon fiber mattes are draped over. The carbon fiber is then reinforced by an epoxy resin, which over a 24 hour period is hardened. The surface is then polished, and finally resealed by adding another layer of epoxy resin. The wing is then bolted to the end plates through the two metal brackets inserted into the wing's ends.

  \subsection{Polystyrene Moulds}

  \begin{figure}
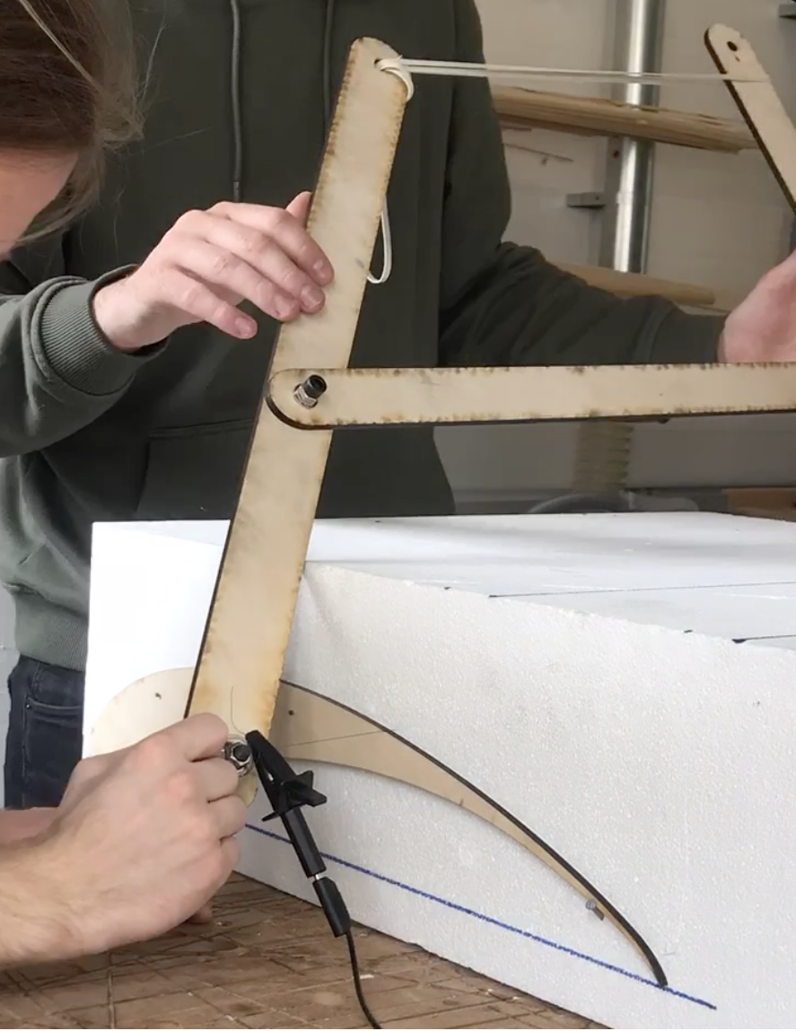
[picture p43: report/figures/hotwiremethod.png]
    
    \caption{The hot wire melts the styrofoam while sliding along the wooden template.}
    \label{fig:hotwire}
  \end{figure}

  The moulds for the wings were chosen as positive moulds, meaning polystyrene moulds of the actual wings were cut out and overlaid with resin coated carbon fiber. In order to do this, we devised a hot wire-based specialized tool for the job. This can be seen in figure \ref{fig:hotwire}, where a $\SI{0.3}{\milli\metre}$ heat resistant
   wire was used at $\SI{12}{\volt}$ drawing $\SI{2.5}{\ampere}$ over a cutting length of $\SI{600}{\milli\metre}$. In order to get the correct airfoil shapes, the MSHD airfoil profile was lasercut out of 3mm plywood. The wooden profile is then mounted on the sides of the polystyrene block, where the hotwire is pulled across in a timely fashion. In order to produce a smooth surface, two people have to move very coordinated. Going too slow leaves deep melting lines, and moving too fast makes the hotwire ''slack'' in the middle as it does not have enough energy to melt the polystyrene quick enough, causing the airfoil profile to be skewed.

  All hotwire cutting was done by hand over several days, and we owe a special thanks to our sponsor DTU Skylab for providing the polystyrene blocks.

  \subsection{Hand Layup}

    \begin{figure}
      
      \caption{Steffan and Nicolai performing a hand layup of the carbon fiber mats around a polystyrene foam core.}
      \label{fig:handlayup}
    \end{figure}

    The finished positive moulds are used both as moulds where carbon fiber is applied on, as well as foam cores that reinforce the structure. The moulds are then placed inside the negative forms of the moulds, where carbon fiber is draped over the surface. The epoxy is then applied to the carbon fiber matte by a soft brush, and air is rolled out by spiked rollers. Nicolai Boertman is seen performing this action in figure \ref{fig:handlayup}, putting the final layer on the main element of the rear wing. The white polystyrene mold underneath the carbon fiber is the negative mold, which helps keep the shape when applying to carbon fiber to the other side. After rolling out the epoxy satisfyingly, a plastic tarp is added to the surface and rolled down neatly without air bubbles. This ensures getting a smooth surface, and lets the wing cure in a closed environment.

    \begin{figure}
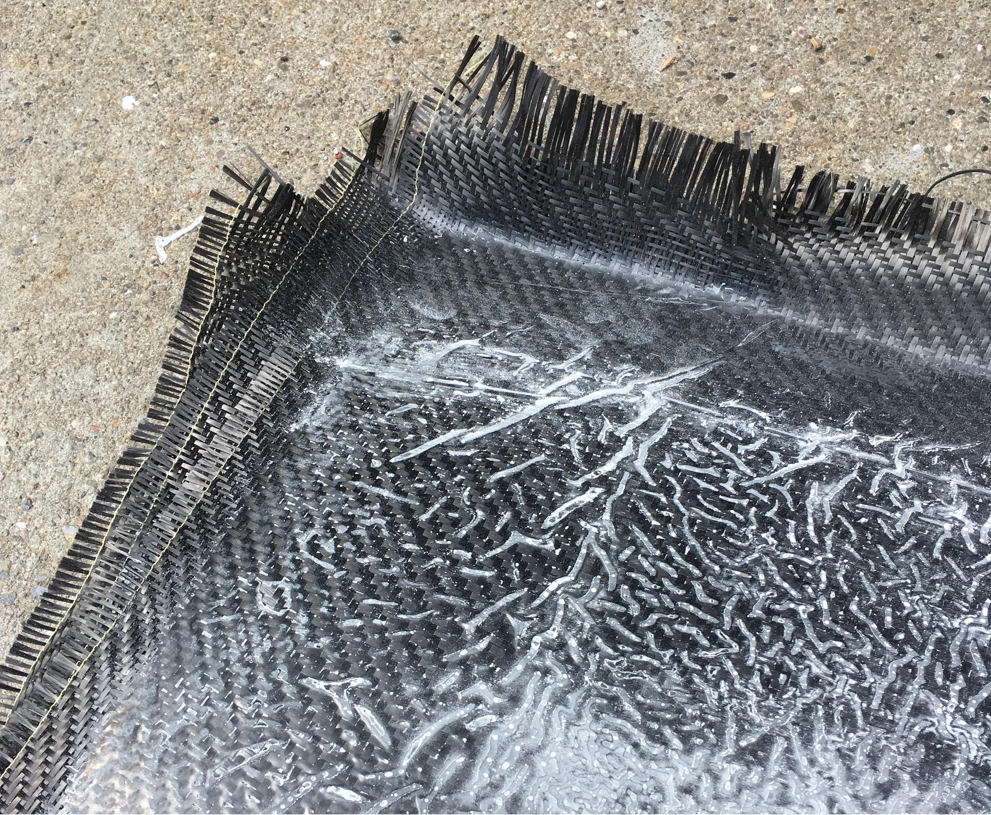
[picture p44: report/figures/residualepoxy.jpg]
      
      \caption{Curing the wing in a flat position lets the resin pool in the center of the wing. This causes the surface to be very rough, potentially causing the boundary layer to trip early. A very unwanted effect that requires mending.}
      \label{fig:roughsurface}
    \end{figure}

    Three methods of curing was attempted:

    \emph{The wing hanging freely with no pressure}: The results was good. No pooling of epoxy, the surface was relatively smooth, but an additional sealing layer had to be applied, as the epoxy had been displaced from the surface. This gave it the surface roughness of the fibers, which is not optimal.\newline
    \emph{The wing laying flat under pressure with the convex shape pointing upwards}: This was highly successful, giving a very smooth surface with the right amount of epoxy covering it. No additional treatment was required.\newline
    \emph{The concave shape pointing upwards}: The results was not good, but workable. The results can be seen in figure \ref{fig:roughsurface}. The epoxy pooled due to gravity forcing the epoxy down towards the center of the cambered wing. Getting a proper surface finish from this is handled in the section below.

  \subsection{Surface Finish}

    Curing \emph{should} occur by securing the wing \emph{vertically} or with the convex shape pointing upwards, as to not let epoxy pool up on the concave surfaces. This knowledge was forgotten on one of the wings, as seen in figure \ref{fig:roughsurface}, where the surface has become very rough due to epoxy pooling. Albeit not optimal, the wing can be salvaged by sanding. The finished product after sanding and preparing the surface is shown in figure \ref{fig:wingaftersanding}. The surface finish is done with a thin layer of extra epoxy. Using a clear lacquer was also investigated, but the reduced durability of the lacquer is not optimal \cite{lacquersucks}. The wing has to survive transport to England, which can damage a soft surface.

    \begin{figure}
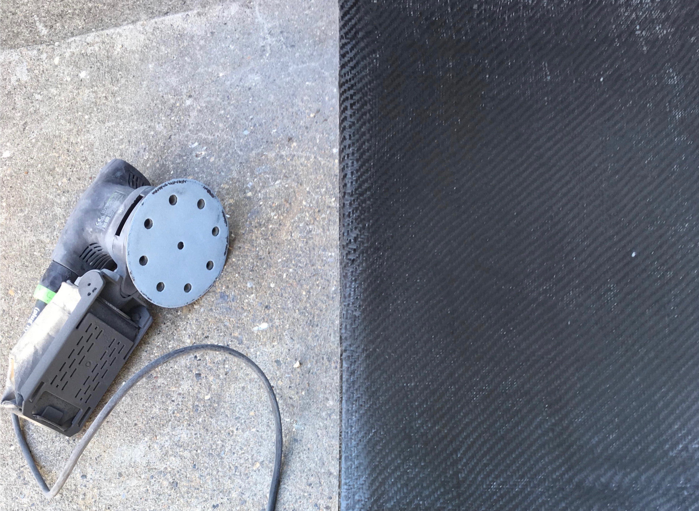
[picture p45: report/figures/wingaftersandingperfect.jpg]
      
      \caption{Sanding the wing clears the surface roughness, but requires a new layer of sealant. Using epoxy or a lacquer was investigated before settling on epoxy.}
      \label{fig:wingaftersanding}
    \end{figure}

  \section{Final Assembly}

    The final assembly of the wing is going to be done in July before competition start. A complete design of the wing is not feasible at this stage, due to many unforeseen changes in how the rear of the car is going to fit together. The wing is not essential for a bare minimum product, which is why the fitting hereof is not a priority for the team as a whole.

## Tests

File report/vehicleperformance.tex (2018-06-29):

% !TEX root = main.tex
\chapter{Aerodynamic Effects on Vehicle Performance}
\label{chap:vehicleperformance}

  The first argument to the importance of aerodynamics is based on two facts: The fact that drag is negligible in regards to the Formula Student vehicle's top speed on straights, and the fact that aerodynamically increasing the vehicle's \emph{effective} mass due to downforce increases tyre grip, which in turn allows for higher cornering velocities.

  The second part of this chapter covers the importance of centering the effective mass increase due to aerodynamic devices close to the center of gravity -- otherwise handling characteristics becomes a function of velocity.

\section{Drag Effects on Straights}
\label{sec:topspeed}

  \begin{figure}
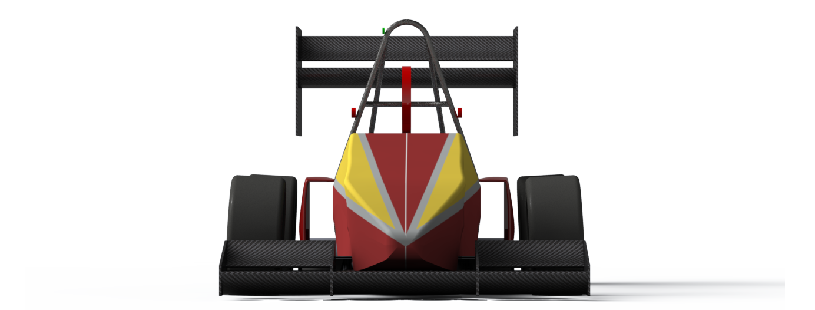
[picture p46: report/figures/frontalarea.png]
    \makebox[\textwidth][c]{}
    \caption{Frontal area of the car with a dummy wing inserted into the CAD model, in order to get an estimate of the drag coefficient $C_D$.}
    \label{fig:frontarea}
  \end{figure}

  First, let's explain what makes a car fast, and what parameters we can change to improve the speed of our car. The car's acceleration can be described by Newton's second law as:
  \begin{align}
    \sum F_x &= m a
    \intertext{Where the sum of forces working in the x-direction (the direction of travel) can be expressed as the force already pertained by the vehicle: The force the motor exerts is given by $F = \frac{P}{\dot{x}}$, where $P$ is the power of the car, minus the drag force:}
    F_D &= \frac{1}{2} C_D \rho \dot{x}^2 A\\
    F_\text{motor} &= m \ddot{x} = \frac{P}{\dot{x}}\\
    \sum F_x &= F_\text{motor} - F_D = \frac{P}{\dot{x}} - C_D \left(\frac{1}{2}  \rho \dot{x}^2 A \right) = 0
    \intertext{Where $C_D$ is the drag coefficient of the vehicle, $\rho$ is the density of the fluid it moves in and $A$ is frontal area of the vehicle. Solving for maximum speed, that is, when the two forces sum to zero:}
    F_\text{motor} &= F_D
    \intertext{As we were interested in the max speed of the car, let's solve for the velocity, giving:}
    \dot{x} &= \left( \frac{2 P}{C_D \left(\rho A \right)}\right)^{\frac{1}{3}}
  \end{align}
  This is assuming we're traveling at terminal velocity -- that is, the point where the $\text{Driving Force} = \text{Friction Force}$. The terminal velocity of the racer is then easily calculated, as the competition restricts the maximum amount of power to $\SI{80}{\kilo\watt}$, and the frontal area of the car is approximated from the CAD drawing seen in figure \ref{fig:frontarea}.

  \begin{align}
    \dot{x}_\text{max} &= \left(\frac{2\cdot \SI{80}{\kilo\watt}}{0.85\left(\SI{1.225}{\kilogram\per\cubic\metre}~ \SI{0.99 }{\square\metre}\right)}\right)^{\frac{1}{3}} = \SI{53.7}{\metre\per\second} = \SI{193.5}{\kilo\metre\per\hour}
    \intertext{however, given the ruleset a forecasted maximum of $\SI{110}{\kilo\metre\per\hour}$ allows a much larger drag coefficient $C_D$:}
    C_D &= \frac{2 P}{\dot{x}^3 \left(\rho A \right)}
    = \frac{2 \cdot \SI{80}{\kilo\watt}}{(\SI{110}{\kilo\metre\per\hour})^3 \left(\SI{1.225}{\kilogram\per\cubic\metre}~ \SI{0.99}{\square\metre} \right)} = 4.62
  \end{align}
  Thus, the car's top speed will only be limited by a drag factor $>4.62$, which is far above the drag introduced by the aerodynamic devices.

  From this derivation, it is clear that the car's abilities at maximum speeds far exceed the requirement of the track. Therefore, the next step is to improve cornering speeds which depend strongly on the tyre's grip on the surface of the road \cite{jkatz}.

  \section{Downforce Effects on Cornering}

    Shown before, drag does not limit the car's performance on straights. During cornering, drag is not an issue either, but the grip of the tyres limits the maximum velocity before the vehicle loses traction due to the centripetal force which is given by: \cite{taylor2005classical}
    \begin{align}
      F_\text{centripetal} &= \frac{m\dot{x}^2}{r}
      \intertext{where $r$ is the distance to the center of the cornering circle. The frictional force the car exerts due to downforce and tyre grip is given by:}
      F_\text{friction} &= \mu F_\text{normal} \label{eq:downforcetocorneringspeed}
      \intertext{where the normal force is given by both the weight and (negative) lift of the car, which serves as an effective mass increase:}
      F_L &= \frac{1}{2}C_L \rho  A \dot{x}^2\\
      F_\text{friction} &= \mu \left(mg + \frac{1}{2} C_L \rho  A \dot{x}^2 \right)
      \intertext{The vehicle will lose traction when the frictional force is less than the centripetal force.}
      \frac{m\dot{x}^2}{r} &> \mu \left(mg + \frac{1}{2} C_L \rho  A \dot{x}^2 \right)
      \intertext{Giving the maximum velocity for a given corner radius before the car skids out:}
      \Rightarrow \dot{x} &< \left(\frac{2\mu mg r}{m - \mu C_L \rho r  A}\right)^{\frac{1}{2}}
    \end{align}
    Again, the forecasted variation in radii of corners is prescribed by the rules to be between \SIrange{3}{50}{\metre}\cite{FSrules18}. Plotting this for various $C_L$ values between $1.5$ to $2.6$ \cite{CLvalues}, assuming $m=\SI{300}{\kilogram}$, $\mu = 1.5$ \cite{tyrefriction} and $A = \SI{0.99}{\square\metre}$ as previously used. The result can be seen in figure \ref{fig:cornerspeedvslift}.
    \begin{figure}
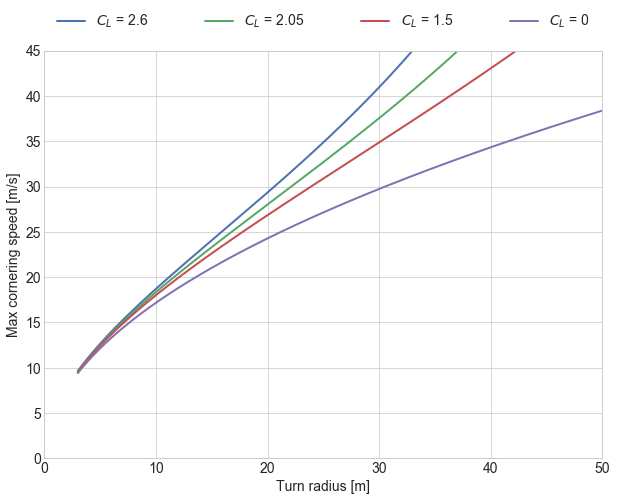
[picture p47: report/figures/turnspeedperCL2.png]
      \makebox[\textwidth][c]{}%
      \caption{Cornering speed as a function of turn radius for various lift coefficients.}
      \label{fig:cornerspeedvslift}
    \end{figure}

\section{Load Distribution}

  The scope of this thesis is not to incorporate a full aerodynamic package, but a quick overview of load distribution is essential to understanding the behaviour of the car.

  The effective mass added from negative lift depends on the lift coefficient. It is evident that different items on the car carry different lift coefficients, thus making the lifting forces over the cars length a function of relative speed. For the unexperienced driver, this is not easily managed as handling characteristics change with velocity. Therefore, it is desirable to have the aerodynamic center of pressure close to the car's center of gravity, in order to have similar handling at all velocities. While this is not handled in this thesis, it is ideal for future iterations and essential for a full aerodynamical package.

%Check https://uta-ir.tdl.org/uta-ir/bitstream/handle/10106/24176/Merkel_uta_2502M_%2012503.pdf?sequence=1

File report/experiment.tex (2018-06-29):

% !TEX root = main.tex
\chapter{Wind Tunnel Experiment}
\label{chap:experiments}
  Verifying the simulated aerodynamic effects is imperative to verify the numerical analysis. In order to assess the reliability of the previously mentioned simulations, a physical measurement of the pressure along the down-scaled wing will provide results for comparison. When conducting tests on models, knowing how the flow behaves on different length scales and at different velocities is a requirement. Accordingly, this chapter starts with discussing the fluid theory behind the experimental setup.

  Measurements and tests have been carried out at the DTU Wind laboratory's Red wind tunnel with the help of our supervisor Robert Flemming Mikkelsen the 19\textsuperscript{th} to the 20\textsuperscript{th} of June.

\section{Aerodynamical Theory}

  The theories explaining how fluid effects scale between varying wing sizes is explained, in order to justify using a down-scaled model as evaluation to a real size wing.

  \subsection{Similarity of Flows}
  \label{sec:similarflows}

    In order to perform tests on the rear wing, it has to be scaled down to fit inside the wind tunnel. This reduces the physical size of the wing, which under equal circumstances changes the flow around it. In order to correctly emulate the simulated flow inside a wind tunnel, the Reynolds number of the full scale flow and the model scale flow has to be the same.
    \begin{align}
      \text{Re}_\text{m} &= \text{Re}\\
      \intertext{Mathematically, the Reynolds number are defined as:}
      \text{Re} &= \frac{u L}{\nu}
    \end{align}
    where $u_\infty$ is the velocity of the fluid in motion, $L$ is the characteristic length and $\nu$ is the kinematic viscosity of the fluid.

    For a down-scaled model, matching Reynolds number requires an increase in velocity, inversely proportional to the increase in length:
    \begin{align}
      \frac{u_\text{m} L_\text{m}}{\nu} &= \frac{u L}{\nu} \nonumber \\
      \Rightarrow u_\text{m} &= \frac{L}{L_\text{m}} u \label{eq:windtunnelspeed}
    \end{align}

    Given the nature of the competition, the average cornering speeds are around $\SI{55}{\kilo \meter \per \hour} = \SI{15.28}{\metre\per\second}$, which is where downforce is of most importance. The desired velocity in the wind tunnel for the scale model can be found from equation \ref{eq:windtunnelspeed}:
    \begin{align*}
      u_\text{m} &= \frac{\SI{0.6}{\metre}}{\SI{0.15}{\metre}} \SI{15.28}{\metre\per\second} = \SI{61.12}{\metre\per\second}
    \end{align*}

    Which in accordance to the range of the Red wind tunnel.

\section{Equipment}

  The equipment required for performing a wind tunnel test can be seen below:
  \begin{itemize}
    \item The Red wind tunnel ($\SIrange{60}{65}{\metre\per\second}$)
    \item 1/4 scale wing
    \item Syringe inserts for pressure taps
    \item Rubber tubing
    \item Strain gauge for lift
  \end{itemize}

  The instrumentation and the Red wind tunnel is described below, along with a thorough description of the scale wing designed and produced for the experiment.

  \subsection{Instrumentation}

    Instrumentation to perform the experiments were graciously provided to us by DTU Wind Energy. The following contains a description of the wind tunnel, data-logging devices and software used to perform the measurements.

    \textsc{The Red Wind Tunnel}

      The red wind tunnel is an open loop wind tunnel located at DTU Lyngby. A picture of the wind tunnel with our supervisor Robert Mikkelsen can be seen in figure \ref{fig:theredwindtunnel}. It measures $\SI{0.5}{\metre} \times \SI{0.5}{\metre} \times \SI{1.3}{\metre}$ in the test section, with a maximum wind speed of \SI{65}{\metre\per\second}. The wind tunnel functions in low Reynolds number, which fits with the chosen MSHD aerofoil.

      \begin{figure}
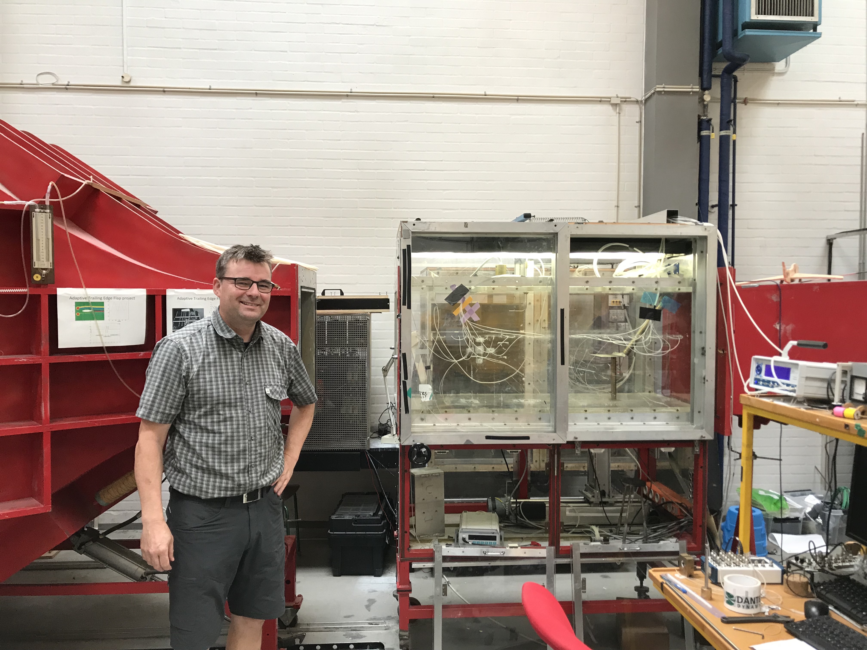
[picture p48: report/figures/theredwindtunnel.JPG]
        
        \caption{Robert Mikkelsen posing in front of the Red wind tunnel. To the left is the air inlet, followed by the test section.}
        \label{fig:theredwindtunnel}
      \end{figure}

    \textsc{Pressure Measurements}

      The Red wind tunnel is equipped with data logging equipment measuring up to 64 pressure probes on a wing profile, the Angle of Attack (AOA), a force gauge measuring the lift forces, a pitot rake measuring the pressure in the wing's wake, the dynamic pressure in the wind tunnel, the operational speed of the wind tunnel, the air density and the time of measurement. The measurement equipment was connected to the data-logging software LabVIEW on a nearby computer.

  \subsection{Manufacturing the 1/4 Scale Rear Wing}

    When producing the small scale model, obstruction of the total area has to be taken into account. The blockage ratio is optimally below $5\%$, with up to $10\%$ compensation. Problematically, getting pressure outlets out of a very small wing is very difficult, and drilling pressure taps along the leading edge also proves to be tedious if made too small. Therefore, a quarter scale wing was chosen with a frontal area of $\SI{0.01375}{\metre\squared}$. Given the tunnel area of $\SI{0.25}{\metre\squared}$, that gives us a blockage ratio of $5.5\%$ - just slightly above the recommended obstruction ratio.

    \begin{figure}
      
      \caption{Blueprints of the centrepiece of the wing containing the pressure taps for generating a pressure distribution profile.}
      \label{fig:scalewingblueprint}
    \end{figure}

    \begin{figure}
      \begin{subfigure}[b]{\textwidth}
        
        \caption{Blueprints of the right section of the wing.}
        \label{fig:scalewingblueprintright}
      \end{subfigure}

      \begin{subfigure}[b]{\textwidth}
        
        \caption{Blueprints of the left section of the wing with a pocket allowing pressure tubes to be fed through. Additionally fitted with an $\diameter \SI{8}{\milli\metre}$ H7 hole for mounting the wing vertically.}
        \label{fig:scalewingblueprintleft}
      \end{subfigure}
    \end{figure}

    \begin{figure}
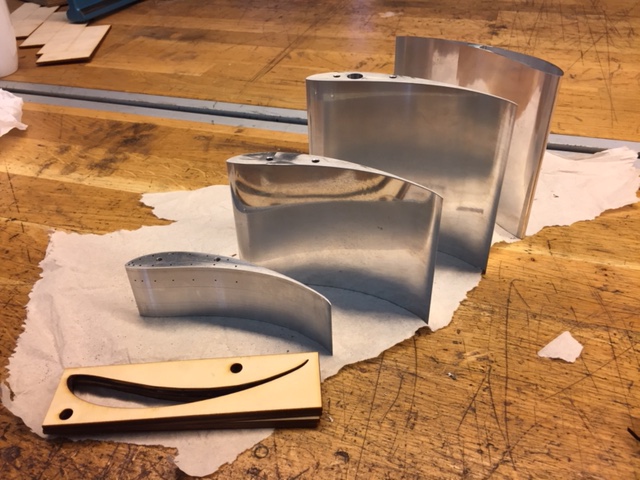
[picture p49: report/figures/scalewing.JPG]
      
      \caption{Pieces of the downscaled wing before assembly. Additional H7 holes had to be drilled in order to mount the wing to the force gauge securely.}
      \label{fig:scalewingparts}
    \end{figure}

    After the initial analysis of airfoils, this design was chosen based on preliminary research. From \cite{winginitialangle}, a rule of thumb for multi element design is that the first element should be around $70\%$ of the total chord length, and the second element around $30\%$. From \cite{jkatz}, the initial position of the elements was chosen. Having the perfect position is not essential, as the experiment is a simply a verification method of the computational method, which will be used to optimize the final design.

    The 1/4 scale rear wing was machined at Philips Lighting by Rasmus Himborg based on the technical drawings presented in the following section.

    \subsubsection{Blueprints}

      The wing requires a series of pressure taps for the measurements needed. 15 holes have to be made along the very narrow wing profile to measure the pressure on the wing's surface. The pressure taps have to be $\diameter\SI{0.8}{\milli\metre}$ on the outside, with an inner bore hole with $\diameter\SI{1.2}{\milli\metre}$ to have a syringe inserted. The wing needs to be separated into smaller parts, as drilling $\diameter\SI{1.2}{\milli\metre}$ pressure inlets throughout the entire wing is very difficult. Thus, the large wing is dissected into three parts. A central part with 15 pressure taps, and two regular wings with holes for pressure tubes to escape. The left section contains a H7 hole for fitting the wing in the wind tunnel and leading the pressure tubes to the pressure transducer. The right wing is a basic wing with holes for mounting. These two parts can be seen in figures \ref{fig:scalewingblueprintright} and \ref{fig:scalewingblueprintleft}. Aligning the three wing sections has to be fairly accurate. The center wing thus carries threaded holes, and the adjacent wings has M4 holes where a threaded rod can align the wings securely. The final design of the centrepiece can be seen in figure \ref{fig:scalewingblueprint}.

      Material selection is based on the ease of machinability - a CNC-miller was provided to us, along with ample amounts of aluminium. This scale wing is not to be used in the actual race car, so weight is not a concern. Construction of the 1/4 scale wing is not trivial. High precision is required for the surface finish, and the pressure taps have to be small in diameter: $\diameter\SI{0.8}{\milli\metre}$ and very deep. This is not an ordinary task and requires specialized tooling.

      The manufactured model wing can be seen in \ref{fig:scalewingparts}, taken shortly after receiving the parts back from Rasmus Himborg. The width of the centrepiece is based around the fact that potential upstream interference from misalignment of the wing profile sections would not cause issues around the pressure taps. %Emmons box

      \textsc{3D-printed parts}

        Due to machining cost and production time, the second element was 3D-printed on A Zortrax M200 3D printer at DTU Skylab. The two 3d printed parts were glued together using instant glue.

      \textsc{Assembly}

      \begin{figure}
        
        \caption{Down-scaled wing assmembled with a zoom in on the pressure taps. The length of the entire wing is approximately $\SI{250}{\milli\metre}$ with a total chord length of $\SI{150}{\milli\metre}$.}
        \label{fig:scalewing}
      \end{figure}

      In figure \ref{fig:scalewing} the down-scaled wing post-production with pressure tubes inserted can be seen with pressure-taps along the centrepiece. The wing is assembled by laser cutting the two end plates with holes for mounting, as well as the H7 mounting hole and exits for the pressure tubes.

      In order to strengthen the construction and smoothen the surface, the 3D-printed rearwing was reinforced using red tape (as seen in figure \ref{fig:scalewing}), and is additionally supported by a wooden centrepiece holding the two wings together. Lastly, the small wing is reinforced further by attaching screws through the end plate, ensuring the wing does not rotate.

\section{Experimental Procedure}

  The model wing's $\diameter\SI{8}{\milli\metre}$ hole is fitted with a rod at the end as seen to the left in figure \ref{fig:scalewing}, which is then mounted to the force gauge at the bottom of the wind tunnel. It is important the wing is placed as close to true level, in order to not get a skewed angle of attack initially \cite{truelevel}. The pressure measurement tubes are passed through a hole in the bottom of the wind tunnel's test section. Connection is established to the LabVIEW software running on a nearby computer. A picture of the data collection UI can be found in appendix \ref{app:labviewview}.

  The wing is positioned with a $0^\circ$ angle of attack. Measurements are taken with $\SI{10}{\metre\per\second}$ increments in the range of $\SIrange{10}{60}{\metre\per\second}$, with an angular sweep at $\SI{20}{\metre\per\second}$ and $\SI{40}{\metre\per\second}$ to compare the optimum angle of attack with literature.

  However, due to the wing covering a relatively large area of the wind tunnel, the final test could only go to $\SI{59.2}{\metre\per\second}$, which corresponds to $\SI{14.8}{\metre\per\second}$ or $\SI{53.3}{\kilo\metre\per\hour}$. Albeit slightly lower than optimal, it is not far out of the proposed range.

\section{Results}

  The results from the experiment is divided into two parts: A comparison with the theoretical lift values of the downscaled wing, and a comparison with the simulated results. The simulated results will be shown in section \ref{sec:simulationcomparison}, while the comparison to theory can is shown below.

  \begin{figure}
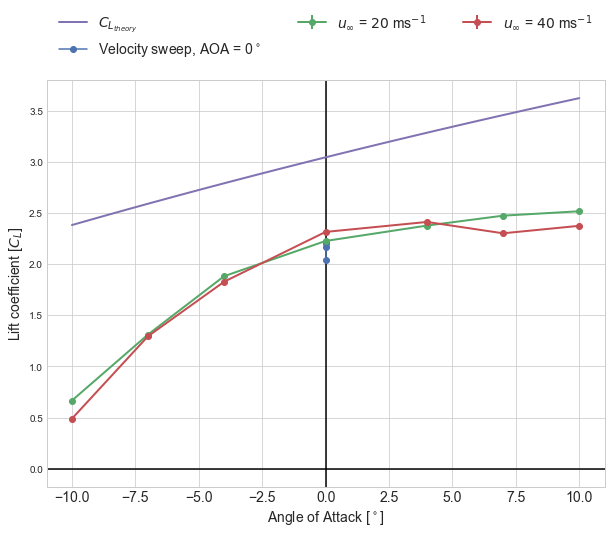
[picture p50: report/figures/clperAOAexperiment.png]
    
    \caption{The lift coefficient plotted as a function of the wing's overall AOA. The wing's own angle of attack is $35^\circ$, which is beyond the theoretical optimum as seen in figure \ref{fig:AOAofairfoils}.}
    \label{fig:clperAOAexperiment}
  \end{figure}

  The theoretical lift coefficient at of the scale wing using a total AOA of $\alpha = 37^\circ$, an effective additional AOA from the wing's camber of $\alpha_{L_0} = 0^\circ$ and equation \ref{eq:CL} is found to be:
  \begin{align*}
    C_L &= \frac{C_{L0}}{1+\frac{C_{L0}}{\pi \AR}}
    \intertext{and remember that:}
    C_{L0} &= 2\pi (\alpha + \alpha_{L_0})\\
    \Rightarrow C_L &= \frac{2\pi \left(\frac{38\pi}{180}\right)}{1+\frac{2\pi \left(\frac{38\pi}{180}\right)}{\pi \frac{\SI{250}{\milli\metre}}{\SI{150}{\milli\metre}}\left(1+1.9\frac{\SI{175}{\milli\metre}}{\SI{250}{\milli\metre}}\right)}} = 3.1
  \end{align*}

  Comparing the theoretical lift to the lift coefficients found by the experiments is seen in figure \ref{fig:clperAOAexperiment}. The purple line is the theoretical lift, where the wing's angle is swept between $-10^\circ$ and $10^\circ$. The measured lift is slightly lower than the theoretical, which may be explained by the end plate's effect on aspect ratio. The downscaled wing has a very large $\AR$, where the end plates extend far below the bottom of the wing. While theoretically beneficial, the effect of the long end plates might not extend all the way up to the wing profile, artificially inflating up the theoretical lift number. Another effect is seen in figure \ref{fig:endplatesbending}, albeit a bit difficult to see, the end plates bend down due to the lower pressure between the endplates. This might have reduced flow underneath the wing, constricting airflow and reducing the overall lift. The deflection was approximately $\SI{10}{\milli\metre}$ on each end plate.

  \begin{figure}
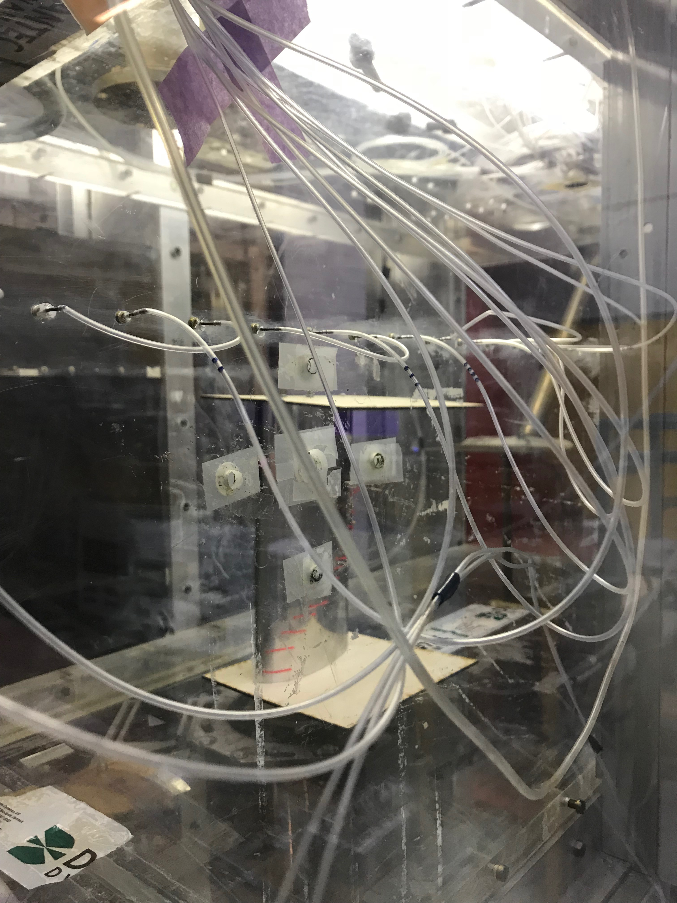
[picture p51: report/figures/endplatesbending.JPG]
    
    \caption{The upper end plate can be seen deflecting slightly downward due to the lower pressure between the endplates.}
    \label{fig:endplatesbending}
  \end{figure}

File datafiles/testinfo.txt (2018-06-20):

NI Setup 
Force gauge og vinkel encoder på NI: USB-6218

Force Gauge er hjemmelavet af Robert - Strain gauge og DIY

25 mm over floor

LabView til målinger af tryk
PSI: Pressure Systems 

1-64: tryk
65 AOA
66:gage
67: flap
68: pdyn
69: Vtun
70: rho
71: tid

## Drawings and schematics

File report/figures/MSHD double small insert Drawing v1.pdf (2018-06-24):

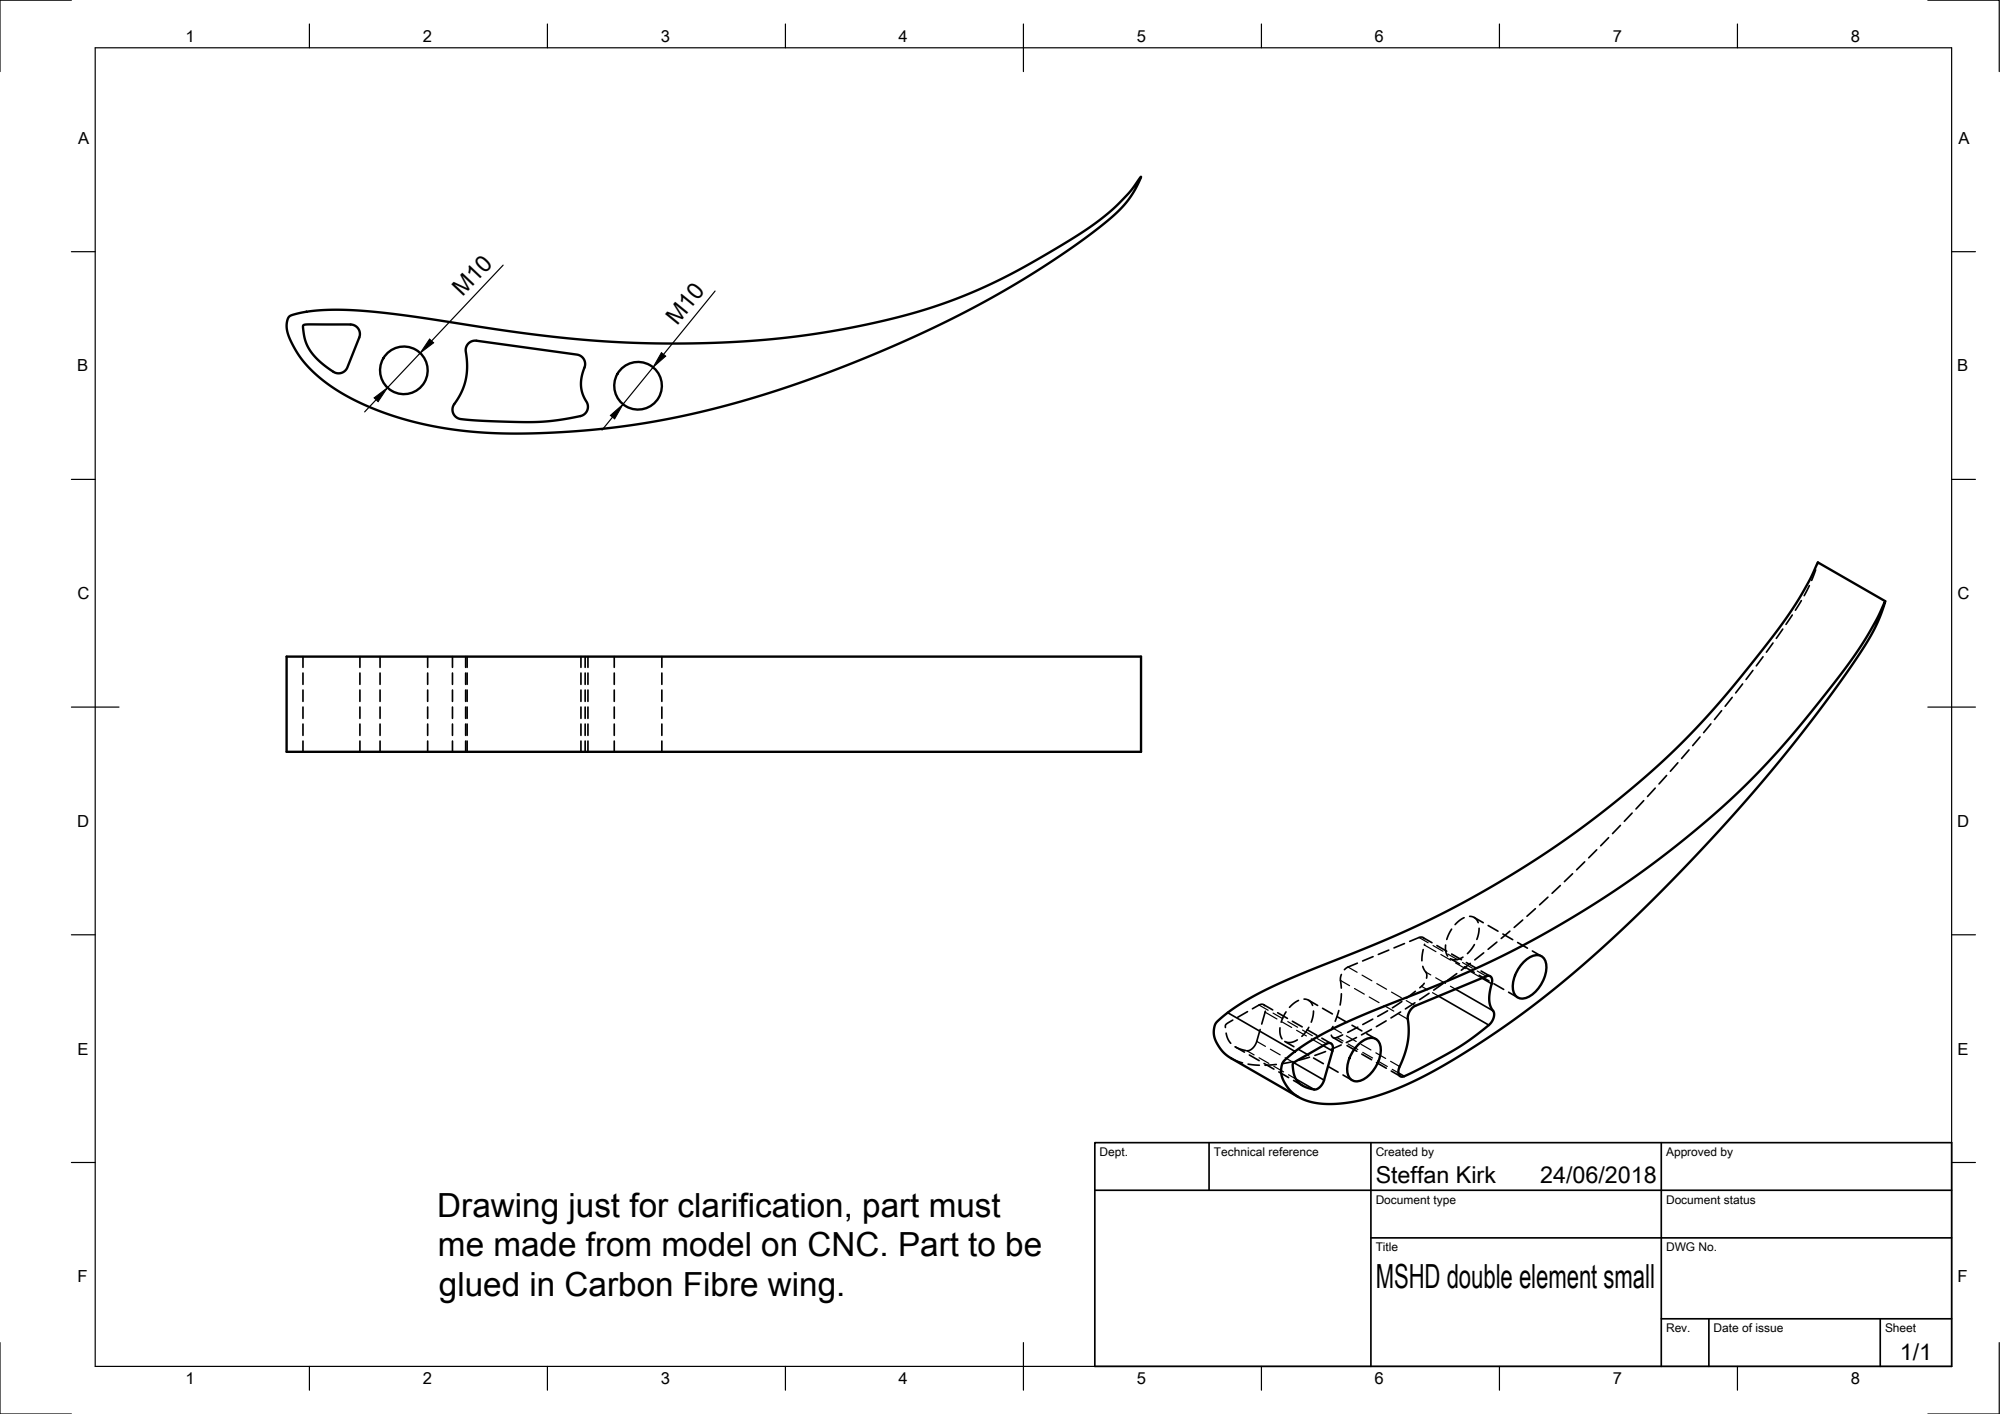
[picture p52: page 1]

Dept. | Technical reference | Created by Steffan Kirk 24/06/2018 | Approved by

Drawing just for clarification, part must
me made from model on CNC. Part to be
glued in Carbon Fibre wing.

Document type | Document status

Title MSHD double element small | DWG No.

Rev. | Date of issue | Sheet 1/1

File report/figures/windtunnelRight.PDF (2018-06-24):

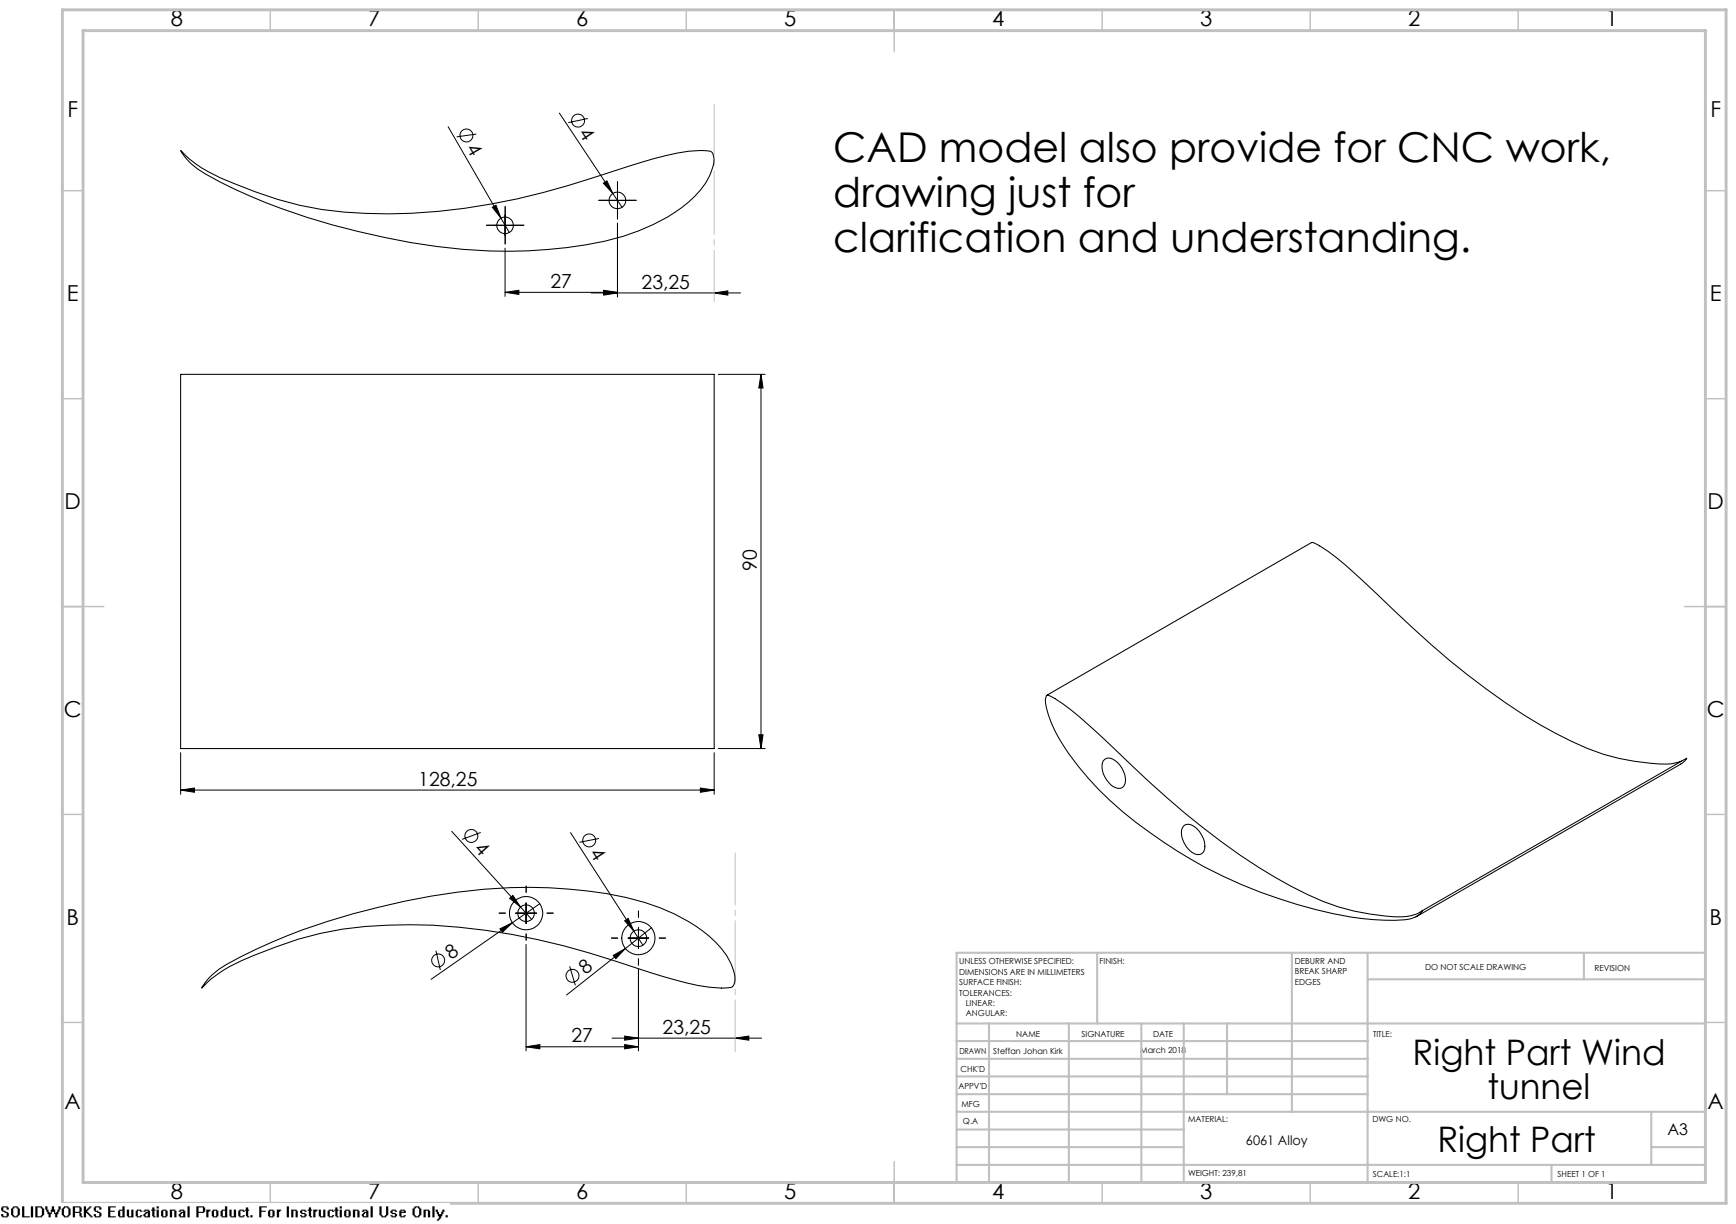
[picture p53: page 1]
FINISH:; DEBURR AND; BREAK SHARP; DO NOT SCALE DRAWING; REVISION; SCALE:1:1; SHEET 1 OF 1; WEIGHT: 239,81

CAD model also provide for CNC work,
drawing just for
clarification and understanding.

UNLESS OTHERWISE SPECIFIED:
DIMENSIONS ARE IN MILLIMETERS
SURFACE FINISH:
TOLERANCES:
LINEAR:
ANGULAR:

NAME | SIGNATURE | DATE | | | | TITLE: Right Part Wind tunnel

DRAWN | Steffan Johan Kirk | | March 2018
CHK'D
APPV'D
MFG
Q.A | | | | MATERIAL: | DWG NO. Right Part | A3 6061 Alloy

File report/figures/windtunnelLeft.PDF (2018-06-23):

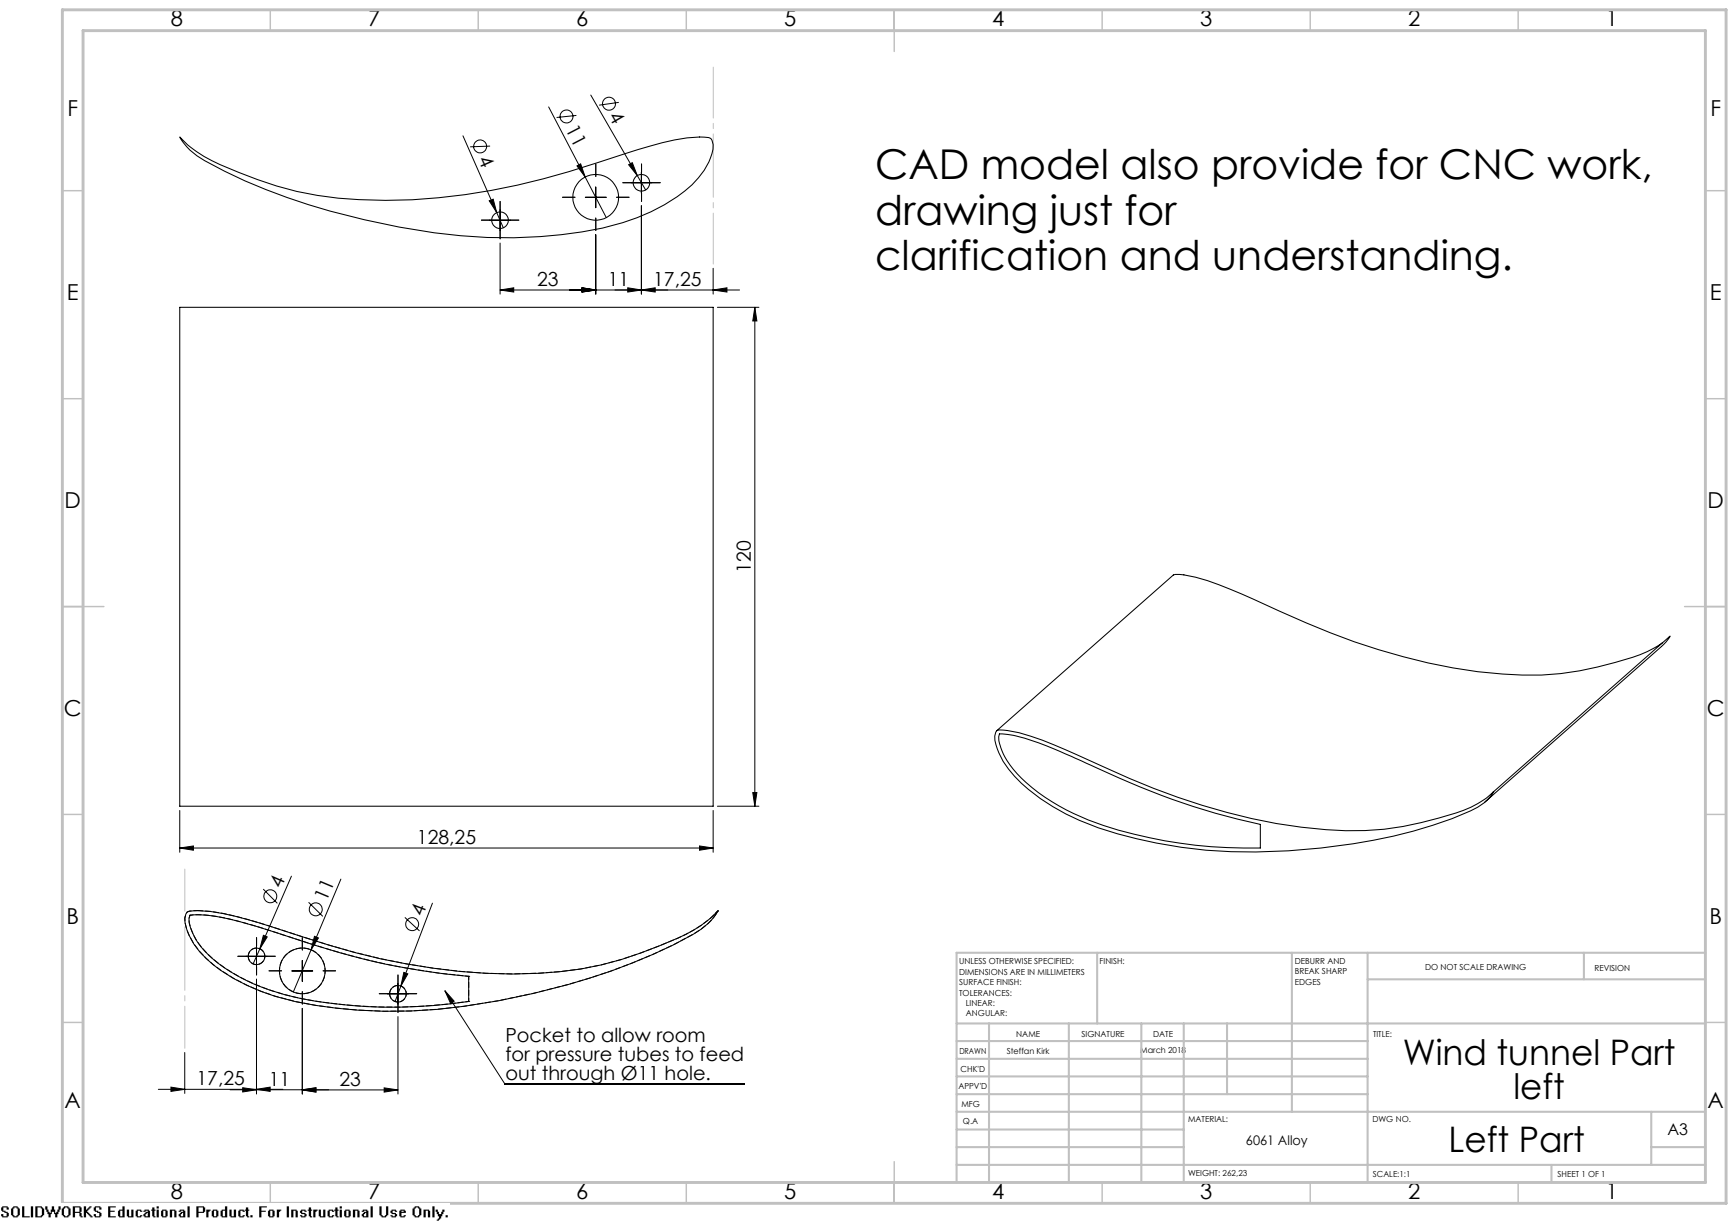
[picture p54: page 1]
FINISH:; DEBURR AND; BREAK SHARP; DO NOT SCALE DRAWING; REVISION; SCALE:1:1; SHEET 1 OF 1; WEIGHT: 262,23; left A

CAD model also provide for CNC work,
drawing just for
clarification and understanding.

UNLESS OTHERWISE SPECIFIED:
DIMENSIONS ARE IN MILLIMETERS
SURFACE FINISH:
TOLERANCES:
LINEAR:
ANGULAR:

Pocket to allow room
for pressure tubes to feed
out through Ø11 hole.

NAME | SIGNATURE | DATE | | | | TITLE: Wind tunnel Part

DRAWN | Steffan Kirk | | March 2018
CHK'D
APPV'D
MFG
Q.A | | | | MATERIAL: | DWG NO. Left Part | A3 6061 Alloy

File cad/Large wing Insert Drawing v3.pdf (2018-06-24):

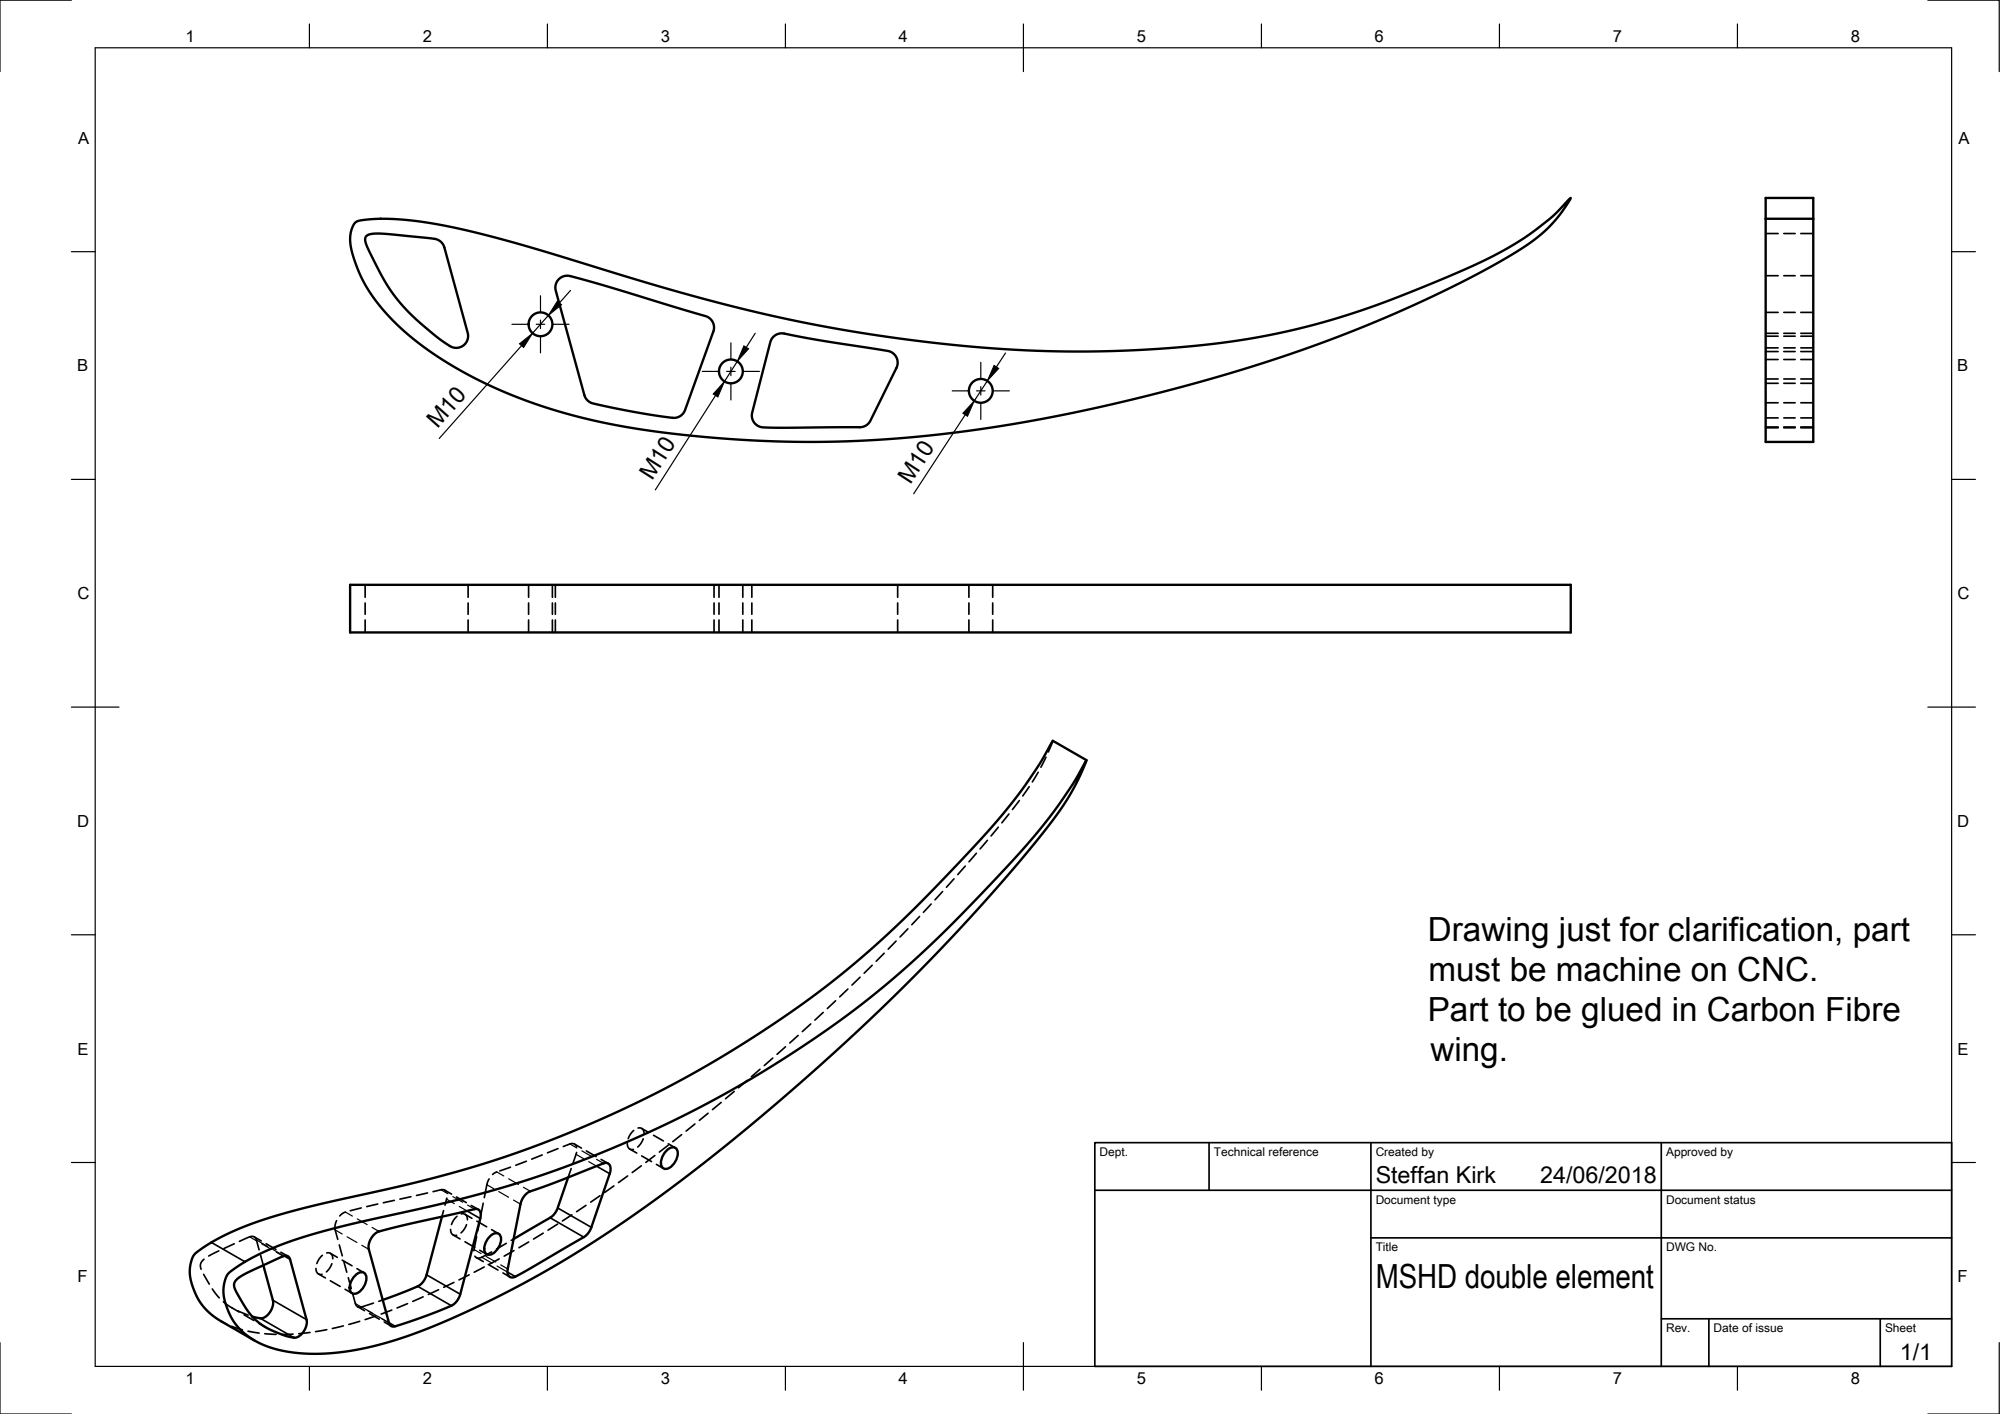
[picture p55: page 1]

Drawing just for clarification, part
must be machine on CNC.
Part to be glued in Carbon Fibre
wing.

Dept. | Technical reference | Created by Steffan Kirk 24/06/2018 | Approved by

Document type | Document status

Title MSHD double element | DWG No.

Rev. | Date of issue | Sheet 1/1

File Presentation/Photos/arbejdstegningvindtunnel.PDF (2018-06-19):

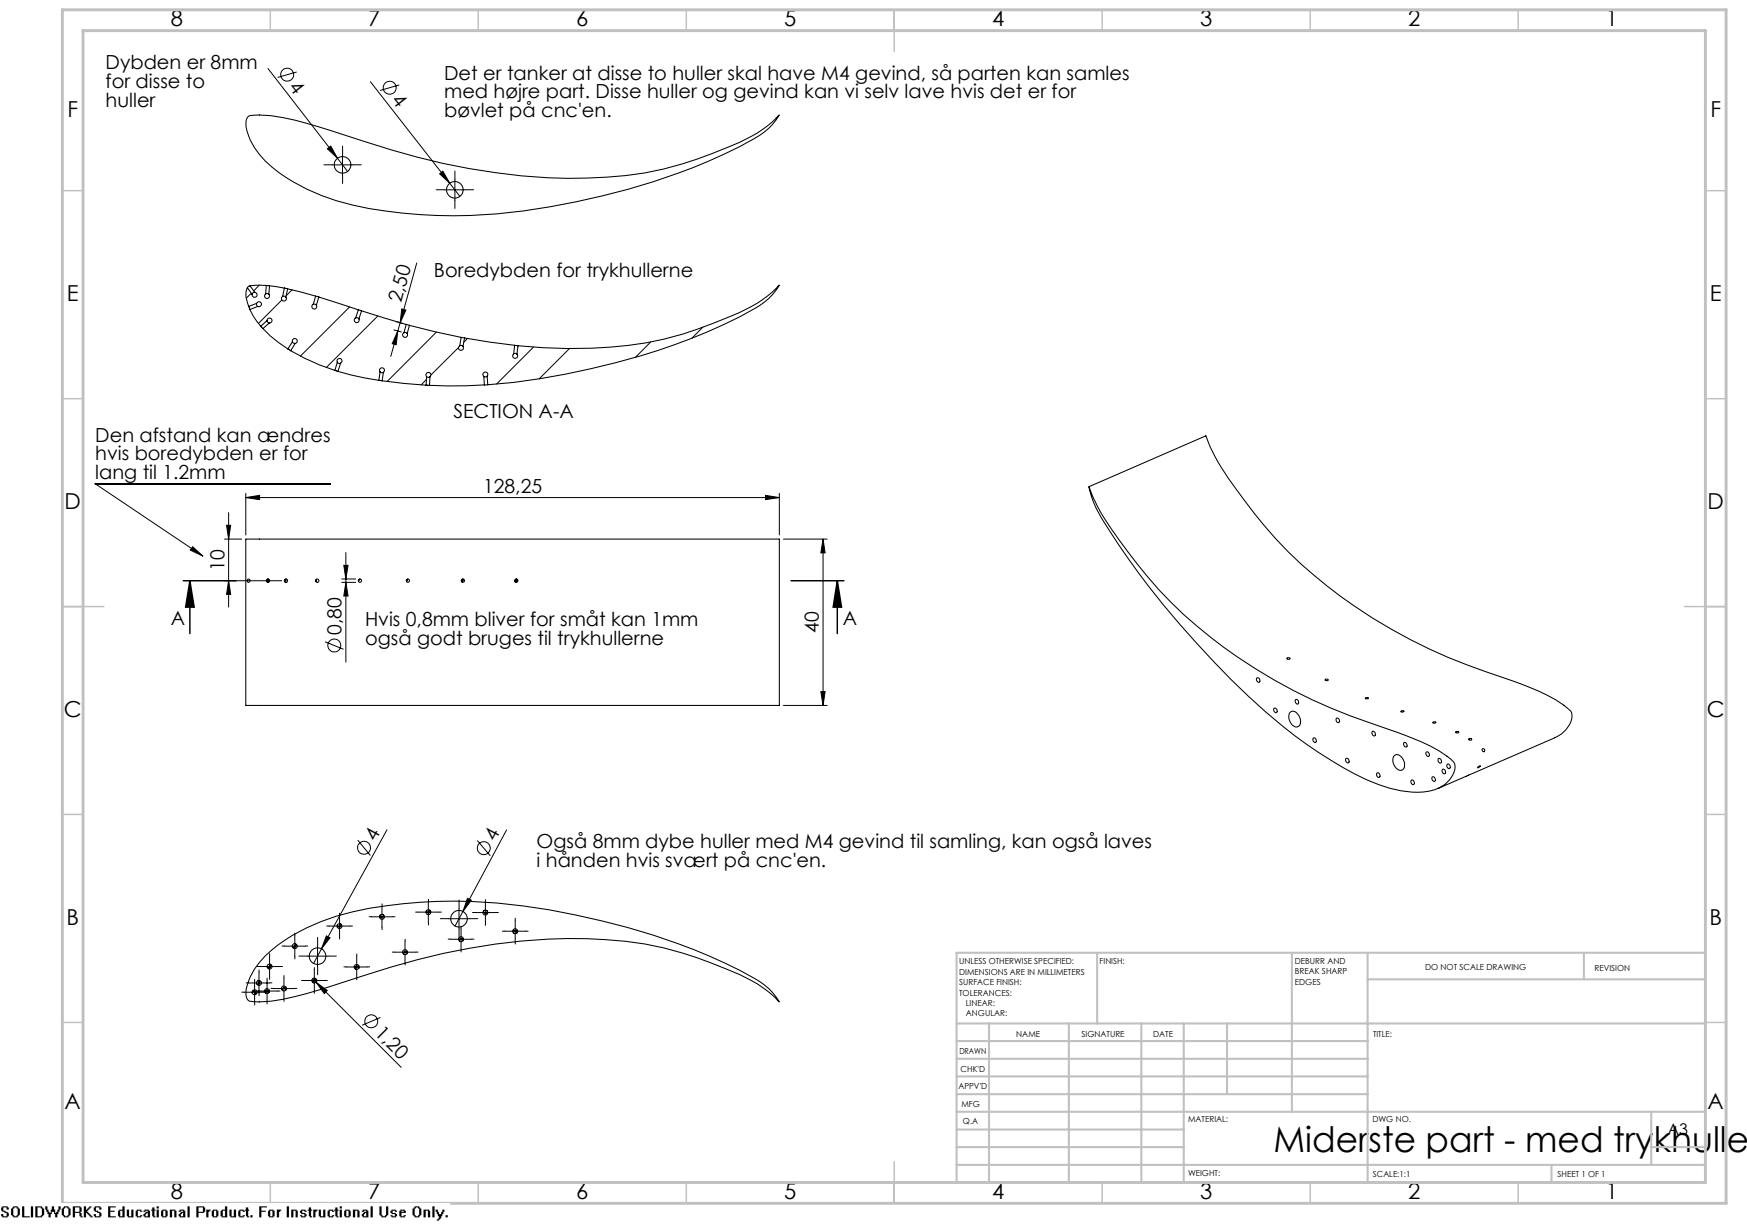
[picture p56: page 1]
Hvis 0,8mm bliver for småt kan 1mm; SECTION A-A; FINISH:; DEBURR AND; BREAK SHARP; DO NOT SCALE DRAWING; REVISION; SCALE:1:1; SHEET 1 OF 1

Dybden er 8mm
for disse to
huller

Det er tanker at disse to huller skal have M4 gevind, så parten kan samles
med højre part. Disse huller og gevind kan vi selv lave hvis det er for
bøvlet på cnc'en.

Boredybden for trykhullerne

Den afstand kan ændres
hvis boredybden er for
lang til 1.2mm

også godt bruges til trykhullerne

Også 8mm dybe huller med M4 gevind til samling, kan også laves
i hånden hvis svært på cnc'en.

UNLESS OTHERWISE SPECIFIED:
DIMENSIONS ARE IN MILLIMETERS
SURFACE FINISH:
TOLERANCES:
LINEAR:
ANGULAR:

NAME | SIGNATURE | DATE | | | | TITLE:

DRAWN
CHK'D
APPV'D
MFG
Q.A | | | | MATERIAL: | DWG NO. | A3

Miderste part - med trykhuller

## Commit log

2018-02-20 slettet rod
2018-03-13 CAD Rearwing uploaded
    [MSHD Single element.SLDPRT, MSHD double element.SLDPRT]
2018-03-15 added subsections
    [MSHD.SLDPRT, MSHD_0st.SLDPRT, airfoil test til starccm.SLDPRT]
2018-06-23 made the paper twosided for print. This is cool
2018-06-24 added pictures of wing inserts
2018-06-25 added datafiles
    [Polar_Graph_1.csv, clperliftdatamaybe.csv]
2018-06-25 redid the ugly figure to be white
    [Polar_Graph_1.csv]
2018-06-25 👌🏿 Har du set den her ?
    Simulation text update
2018-06-26 did some pics
    [V40 3,8mill.csv]
2018-06-26 added csv files of surface pressure
    [V30_pressureSurface.csv, V50_pressureSurface.csv, V60_pressureSurface.csv]
2018-06-28 added CAD of optimized wing
    [MSHD double element optimized.SLDPRT]
2018-06-28 matlab code fix
    [V30_pressureSurface.csv, V50_pressureSurface.csv, V60_pressureSurface.csv]
2018-06-28 did wing deflection
2018-06-29 Lots of simulation text and pictures. Matlab code as well.
    [V40_pressureSurface.csv, s.csv]
2018-06-29 added wing inserts
    [MSHD double element small insert.step, MSHD double element v7 big insert.step]
2018-08-05 added presentqtion files
    [laser vindtunnel.DWG]
